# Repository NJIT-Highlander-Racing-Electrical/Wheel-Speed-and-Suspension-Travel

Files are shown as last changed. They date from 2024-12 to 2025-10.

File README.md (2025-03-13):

# Wheel Speed Sensors

The 2024-2025 vehicle will be integrating sprag clutches into each of the four wheels. This allows for all four wheels to be fully locked together when power is applied, but all four wheels to be fully unlocked while coasting. There are numerous benefits to this setup that are not relevant to this project, however they present the need for individual wheel speed sensors.

These sensors provide data to the suspension subteam about how each wheel is rotating as we move through corners. Along with other vehicle data such as yaw rate, GPS position, vehicle velocity, and steering angle, suspension can get a better picture of how these sprag clutches affect vehicle performance. 

## Potential Designs

With the sprag clutches, the wheels, wheel hubs, and brake rotor all spin together. However, this rotational speed can differ from that of the axles when the clutches are in use. Thus, the sensor must detect either wheel, wheel hub, or rotor rotation.

### Gear Tooth/Ferrous Metal Target Sensor (chosen design)

These type of sensors (like the gear tooth speed sensors we have in stock -- [datasheet here](https://www.jameco.com/Jameco/Products/ProdDS/512401.pdf)) provide a digital output that tracks ferrous metal targets. Their datasheet states that they can be used for detecting holes in rotating discs, such as a brake rotor. Using the brake rotor is ideal for this situation as it does not require adding any additional hardware (such as magnets or a trigger wheel), and it actually reduces the weight of the rotor.

The ones we have in stock are no longer for sale, but [these GS100701](https://www.digikey.com/en/products/detail/zf-electronics/GS100701/280932) could work.

It seems best fit to put four holes in the edge of the rotor that will be detected by this sensor. This sensor can be mounted to a tab/bracket on the caliper, and its distance to the rotor can be adjusted using the sensor's threads/nuts. Because the rotor/caliper distances never change, we can get the sensor close enough to the rotor for accurate readings. 

Adding more than 1 hole in the edge of the rotor allows for more accurate readings. At slower speeds, there will only be a few readings per second which does not paint the most accurate picture of the true wheel speed. More than four holes could be added if the sensor/microcontroller is capable of higher polling rates.

### Permanent magnets and hall effects

If one or more permanent magnets are attached to the wheel, we can use a hall effect to detect when this magnetic field passed by. However, this means we must find a way to securely attach the magnets so that they do not fall off while spinning. Magnets also run the risk of being damaged

### Lasers/Infrared

These could be used to detect when a white stripe passes by the emitter/receiver pair (like the CVT tachometer), but dirt, mud, and other substances can cover the sensors or the sensing target.

# Suspension Travel Sensors

The 2024-2025 vehicle will also be integrating four linear suspension travel sensors. These will give an analog reading which represents the linear position of the shocks. We can then use this data to extrapolate the displacement of the wheels. We are using the LPPS-22-200 sensors from HGSI which have a 200mm stroke. They are essentially just a linear potentiometer, so they can be used with a variety of supply voltages.

## Mapping Suspension Position to Wheel Displacement

Fron two shocks have a motion ratio of 0.75, meaning that a travel 0f 0.75" in the shock would correspond to 1" of wheel displacement

# Electrical Design

These eight sensors (four wheel speed and four suspension travel) can be run to a single microcontroller located inside the vehicle, which can then transmit the data over CAN. Ideally, each wheel speed sensor reading is interrupt-based on the microcontroller so that calculations for RPM can be done as fast as possible. Suspension travel are analog so we will simply poll those for values Each sensor (at the enclosure side) has 3 pin aviation plug connectors. This prevents them from accidentally being connected to the general power/CAN bus while still maintaing our aviation plug standard. At the sensor side, each sensor uses a different, smaller in-line 3 pin connector so that the sensors themselves can be removed and replaced without removing the entire wiring harness.

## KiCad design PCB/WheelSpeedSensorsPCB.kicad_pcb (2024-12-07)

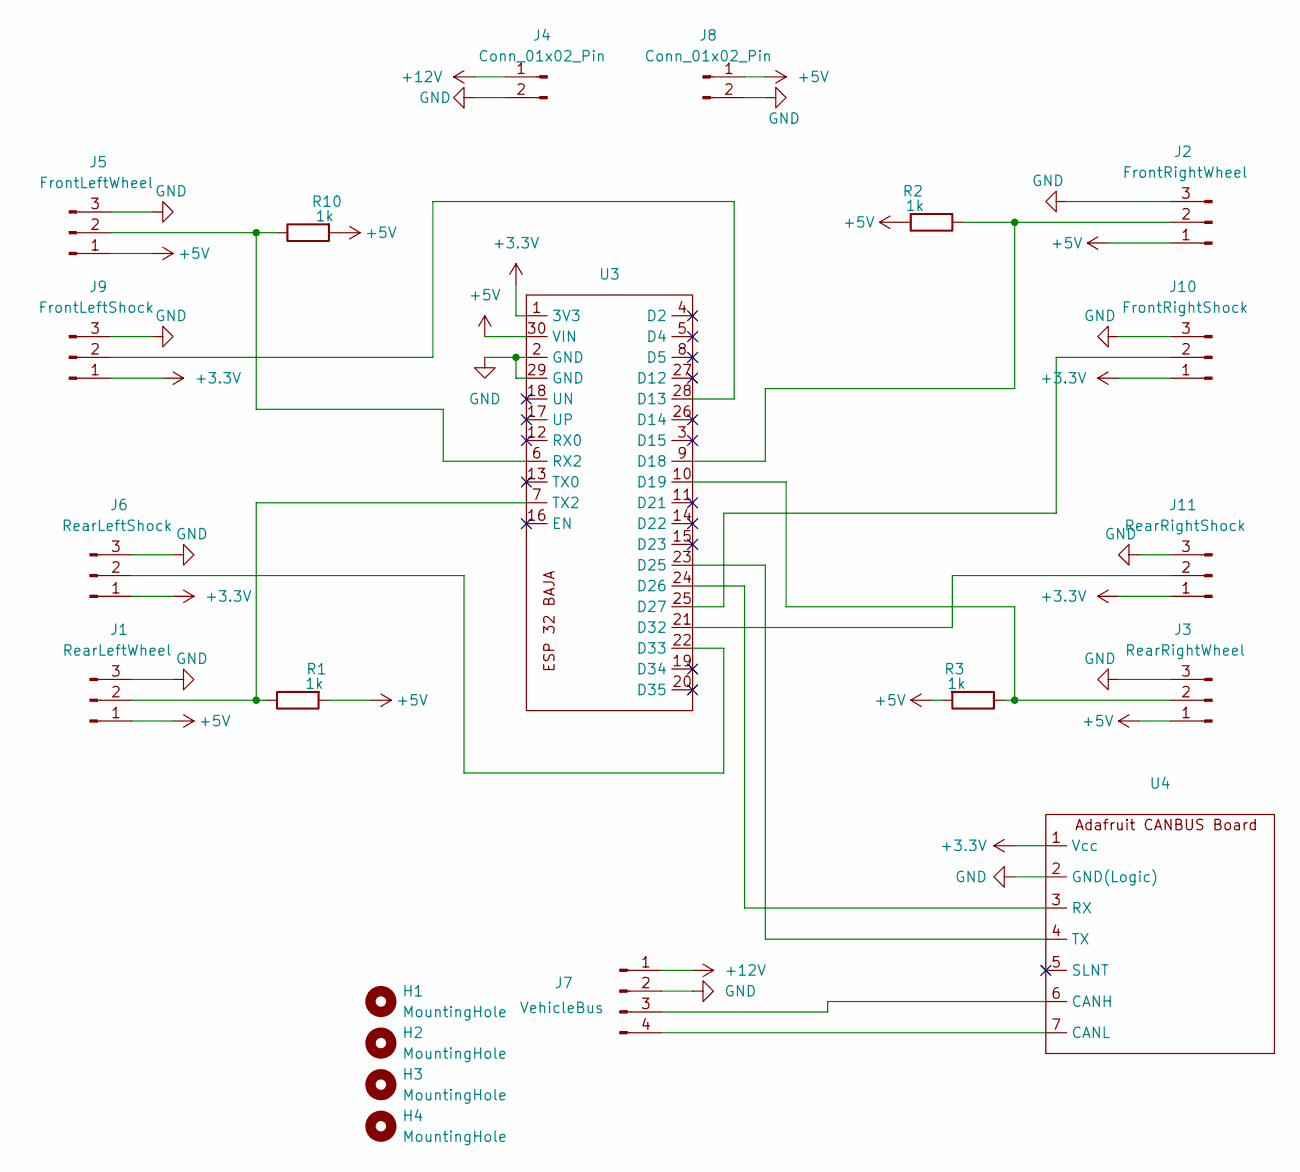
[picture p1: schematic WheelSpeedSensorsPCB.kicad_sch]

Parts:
H1, H2, H3, H4: MountingHole; MountingHole_4.3mm_M4
J1: RearLeftWheel; 3pin
J2: FrontRightWheel; 3pin
J3: RearRightWheel; 3pin
J4, J8: Conn_01x02_Pin; PinHeader_1x02_P2.54mm_Vertical
J5: FrontLeftWheel; 3pin
J6: RearLeftShock; 3pin
J7: VehicleBus; 4pin
J9: FrontLeftShock; 3pin
J10: FrontRightShock; 3pin
J11: RearRightShock; 3pin
R1, R2, R3, R10: 1k; R_Axial_DIN0204_L3.6mm_D1.6mm_P5.08mm_Horizontal
U3: ESP32
U4: 1x7 Connectors

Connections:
+3.3V: J6.1, J9.1, J10.1, J11.1, U3.1 (3V3), U4.1 (Vcc)
+5V: J1.1, J2.1, J3.1, J5.1, J8.1, R1.2, R2.2, R3.2, R10.2, U3.30 (VIN)
+12V: J4.1, J7.1
GND: J1.3, J2.3, J3.3, J4.2, J5.3, J6.3, J7.2, J8.2, J9.3, J10.3, J11.3, U3.2 (GND), U3.29 (GND), U4.2 (GND(Logic))
unnamed: J1.2, R1.1, U3.7 (TX2)
unnamed: J2.2, R2.1, U3.9 (D18)
unnamed: J3.2, R3.1, U3.10 (D19)
unnamed: J5.2, R10.1, U3.6 (RX2)
unnamed: J6.2, U3.22 (D33)
unnamed: J7.3, U4.6 (CANH)
unnamed: J7.4, U4.7 (CANL)
unnamed: J9.2, U3.28 (D13)
unnamed: J10.2, U3.25 (D27)
unnamed: J11.2, U3.21 (D32)
unnamed: U3.23 (D25), U4.4 (TX)
unnamed: U3.24 (D26), U4.3 (RX)

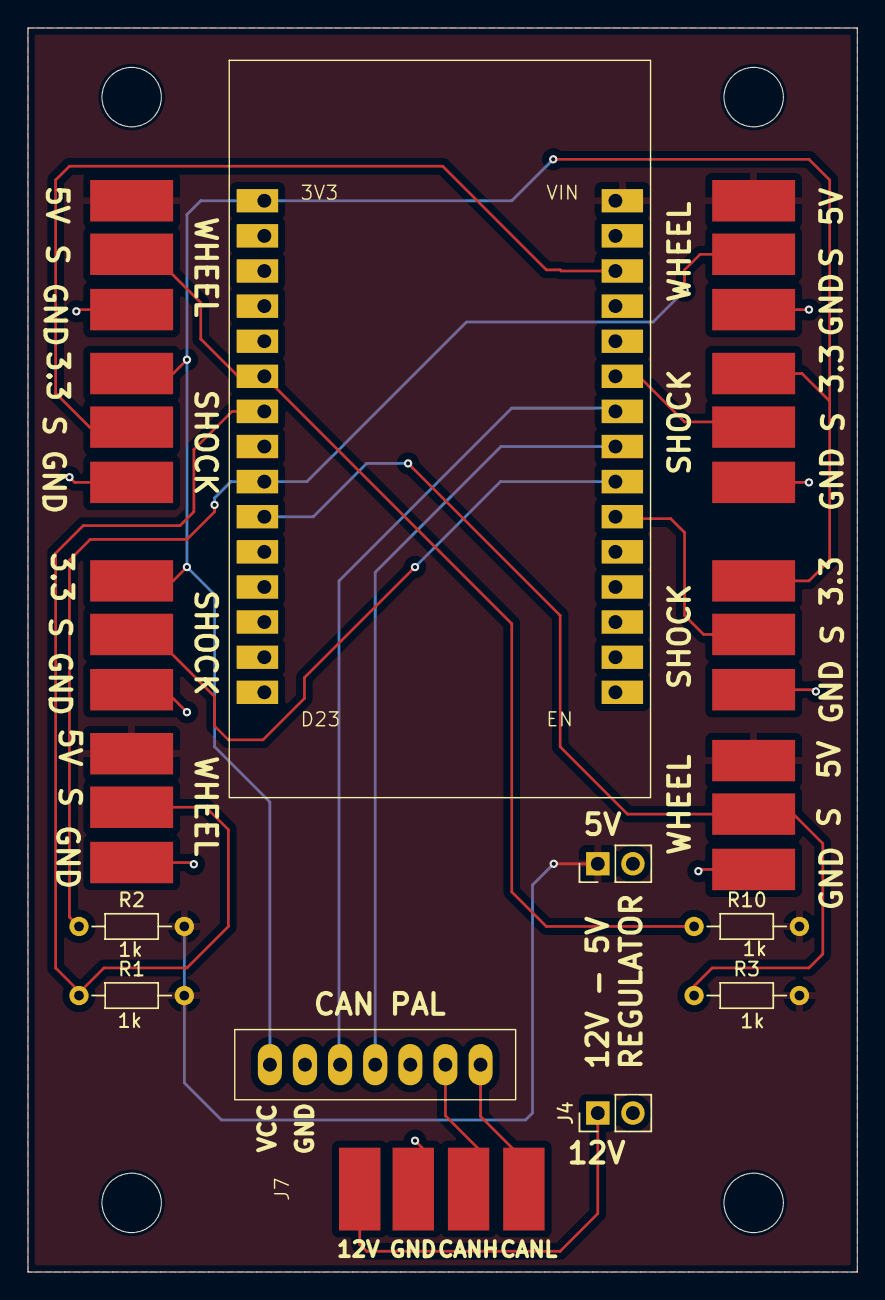
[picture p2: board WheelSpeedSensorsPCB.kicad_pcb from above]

Board: 2 copper layers, 60.0 x 90.0 mm, 21 parts (0 on the bottom side), 16 nets.

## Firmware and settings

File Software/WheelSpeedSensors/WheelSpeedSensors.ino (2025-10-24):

#include "Wheel.h"
#include "Shock.h"
#include "BajaCAN.h"

#define DEBUG_WHEEL false
#define DebugWheelSerial \
  if (DEBUG_WHEEL) Serial

#define DEBUG_SHOCK true
#define DebugShockSerial \
  if (DEBUG_SHOCK) Serial

// Pin definitions for Wheels
const int frontLeftWheelPin = 19;
const int rearLeftWheelPin = 18;
const int frontRightWheelPin = 17;
const int rearRightWheelPin = 16;

// Pin definitions for Shocks
const int frontLeftShockPin = 32;
const int rearLeftShockPin = 27;
const int frontRightShockPin = 33;
const int rearRightShockPin = 13;

// Wheel objects from Wheel.h definition
Wheel frontLeftWheel(frontLeftWheelPin);
Wheel frontRightWheel(frontRightWheelPin);
Wheel rearLeftWheel(rearLeftWheelPin);
Wheel rearRightWheel(rearRightWheelPin);

// Shock objects from Shock.h definition
Shock frontLeftShock(frontLeftShockPin, true, frontLeftShock_restReading);
Shock frontRightShock(frontRightShockPin, true, frontRightShock_restReading);
Shock rearLeftShock(rearLeftShockPin, false, rearLeftShock_restReading);
Shock rearRightShock(rearRightShockPin, false, rearRightShock_restReading);

void setup() {
  Serial.begin(460800);

  delay(100);  // Brief delay for serial to stabilize

  // If the speed sensor detects a metal, it outputs a HIGH. Otherwise, LOW
  // Thus, we want to trigger interrupt on LOW to HIGH transition
  attachInterrupt(digitalPinToInterrupt(frontLeftWheel.sensorPin), frontLeftISR, RISING);
  attachInterrupt(digitalPinToInterrupt(frontRightWheel.sensorPin), frontRightISR, RISING);
  attachInterrupt(digitalPinToInterrupt(rearLeftWheel.sensorPin), rearLeftISR, RISING);
  attachInterrupt(digitalPinToInterrupt(rearRightWheel.sensorPin), rearRightISR, RISING);

  setupCAN(WHEEL_SPEED, 10);  // sendInterval = 10 means that we will be sending 100 times per second

  Serial.println("Wheel Speed System Initialized");
}

void loop() {
  // updateWheelStatus calculates RPM if applicable, checks zero RPM status, and checks for wheelspin/wheel skid
  frontLeftWheel.updateWheelStatus();
  frontRightWheel.updateWheelStatus();
  rearLeftWheel.updateWheelStatus();
  rearRightWheel.updateWheelStatus();

  // Update CAN-Bus variables
  frontLeftWheelSpeed = frontLeftWheel.wheelSpeedMPH;
  frontRightWheelSpeed = frontRightWheel.wheelSpeedMPH;
  rearLeftWheelSpeed = rearLeftWheel.wheelSpeedMPH;
  rearRightWheelSpeed = rearRightWheel.wheelSpeedMPH;

  frontLeftWheelState = frontLeftWheel.wheelState;
  frontRightWheelState = frontRightWheel.wheelState;
  rearLeftWheelState = rearLeftWheel.wheelState;
  rearRightWheelState = rearRightWheel.wheelState;

  // Read shock positions
  frontLeftShock.getPosition();
  frontRightShock.getPosition();
  rearLeftShock.getPosition();
  rearRightShock.getPosition();

  frontLeftDisplacement = frontLeftShock.wheelPos;
  frontRightDisplacement = frontRightShock.wheelPos;
  rearLeftDisplacement = rearLeftShock.wheelPos;
  rearRightDisplacement = rearRightShock.wheelPos;

  // Print data to serial monitor
  DebugWheelSerial.print("frontLeftWheel_Speed:");
  DebugWheelSerial.print(frontLeftWheel.wheelSpeedMPH, 2);
  DebugWheelSerial.print(",");
  DebugWheelSerial.print("frontRightWheel_Speed:");
  DebugWheelSerial.print(frontRightWheel.wheelSpeedMPH, 2);
  DebugWheelSerial.print(",");
  DebugWheelSerial.print("rearLeftWheel_Speed:");
  DebugWheelSerial.print(rearLeftWheel.wheelSpeedMPH, 2);
  DebugWheelSerial.print(",");
  DebugWheelSerial.print("rearRightWheel_Speed:");
  DebugWheelSerial.print(rearRightWheel.wheelSpeedMPH, 2);
  DebugWheelSerial.println();

  DebugShockSerial.print("fl_pos:");
  DebugShockSerial.print(frontLeftShock.wheelPos);
  DebugShockSerial.print(",");
  DebugShockSerial.print("fr_pos:");
  DebugShockSerial.print(frontRightShock.wheelPos);
  DebugShockSerial.print(",");
  DebugShockSerial.print("rl_pos:");
  DebugShockSerial.print(rearLeftShock.wheelPos);
  DebugShockSerial.print(",");
  DebugShockSerial.print("rr_pos:");
  DebugShockSerial.print(rearRightShock.wheelPos);
  DebugShockSerial.println();
}

// ISR implementations - now use the debounced handleInterrupt() method
void frontLeftISR() {
  frontLeftWheel.handleInterrupt();
}

void frontRightISR() {
  frontRightWheel.handleInterrupt();
}

void rearLeftISR() {
  rearLeftWheel.handleInterrupt();
}

void rearRightISR() {
  rearRightWheel.handleInterrupt();
}

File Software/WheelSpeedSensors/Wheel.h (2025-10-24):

const float wheelDiameter = 23;      // Diameter of our wheels in inches
const int targetsPerRevolution = 4;  // number of sensing points per revolution on the wheel
const float wheelSpinThreshold = 5;  // Speed difference (mph) above GPS vehicle velocity where we will declare wheelspin
const float wheelSkidThreshold = 5;  // Speed difference (mph) below GPS vehicle velocity where we will declare skidding

const float rpmToMphFactor = wheelDiameter / 63360.0 * 3.1415 * 60.0;  // When wheel RPM is multiplied by this, it results in that wheel's linear speed in MPH

float vehicleSpeedMPH = 0;  // Since GPS velocity is given in m/s, this converts and stores to MPH

// Minimum time between valid readings (microseconds) - prevents noise/bouncing
// 5000us = 5ms = maximum 720 RPM (well above expected max)
const unsigned long MIN_PULSE_INTERVAL = 5000;

// Maximum time to wait before declaring zero RPM
// At 1 MPH with 4 targets, we get a pulse every ~1.03 seconds
// Allow 2 seconds (2,000,000 microseconds) before declaring zero
const unsigned long ZERO_TIMEOUT_MICROS = 2000000;

enum WheelState {
  GOOD,
  SPIN,
  SKID
};

// Class that defines shared variables and functions between the four wheels
class Wheel {

public:

  int sensorPin;  // GPIO that sensor is hooked up to

  volatile unsigned long lastReadingMicros;
  volatile unsigned long currentReadingMicros;
  volatile bool updateFlag;

  unsigned long nextExpectedMicros;
  
  float rpm;  // variable to store calculated RPM value
  float wheelSpeedMPH;  // calculated wheel velocity for comparison with GPS vehicle velocity

  bool ignoreNextReading;
  bool isFirstReading;

  WheelState wheelState;

  // Moving average for stability
  static const int AVG_SAMPLES = 3;
  float rpmHistory[AVG_SAMPLES];
  int rpmHistoryIndex;
  int rpmHistoryCount;  // Track how many samples we have

  Wheel(int pinNumber) {
    sensorPin = pinNumber;
    unsigned long currentTime = micros();
    lastReadingMicros = currentTime;
    currentReadingMicros = currentTime;
    nextExpectedMicros = currentTime + ZERO_TIMEOUT_MICROS;
    rpm = 0;
    wheelSpeedMPH = 0;
    updateFlag = false;
    ignoreNextReading = false;
    isFirstReading = true;
    wheelState = GOOD;
    rpmHistoryIndex = 0;
    rpmHistoryCount = 0;

    // Initialize RPM history to zero
    for(int i = 0; i < AVG_SAMPLES; i++) {
      rpmHistory[i] = 0;
    }

    pinMode(sensorPin, INPUT);
  }

  // Calculates RPM based on elapsed time between last reading and current time
  // Only runs after respective ISR is triggered
  void calculateRPM() {
    if (!updateFlag) return;

    // Capture timing variables atomically to avoid race conditions
    noInterrupts();
    unsigned long capturedCurrent = currentReadingMicros;
    unsigned long capturedLast = lastReadingMicros;
    updateFlag = false;
    interrupts();

    // Skip first reading - need two points to calculate speed
    if (isFirstReading) {
      noInterrupts();
      lastReadingMicros = capturedCurrent;
      interrupts();
      isFirstReading = false;
      nextExpectedMicros = capturedCurrent + ZERO_TIMEOUT_MICROS;
      return;
    }

    // If we just recovered from zero, ignore this reading (re-establish baseline)
    if (ignoreNextReading) {
      noInterrupts();
      lastReadingMicros = capturedCurrent;
      interrupts();
      ignoreNextReading = false;
      nextExpectedMicros = capturedCurrent + ZERO_TIMEOUT_MICROS;
      return;
    }

    // Calculate time difference (handles overflow correctly since both are unsigned long)
    unsigned long timeDifference = capturedCurrent - capturedLast;
    
    // Sanity check: reject readings that are too fast (noise/bounce filter)
    if (timeDifference < MIN_PULSE_INTERVAL) {
      return;
    }
    
    // Sanity check: reject readings that are impossibly slow (missed timeout somehow)
    if (timeDifference > ZERO_TIMEOUT_MICROS) {
      noInterrupts();
      lastReadingMicros = capturedCurrent;
      interrupts();
      ignoreNextReading = true;
      return;
    }
    
    // Calculate RPM from time difference
    float instantRPM = (1.00 / (float(timeDifference) / 1000000.0)) * 60.0 / targetsPerRevolution;
    
    // Sanity check: 650 RPM = ~45 MPH, reasonable maximum
    if (instantRPM > 650) {
      Serial.print("RPM over 650 rejected: ");
      Serial.print(instantRPM);
      Serial.print(" on pin ");
      Serial.println(sensorPin);
      return;
    }
    
    // Add to moving average buffer
    rpmHistory[rpmHistoryIndex] = instantRPM;
    rpmHistoryIndex = (rpmHistoryIndex + 1) % AVG_SAMPLES;
    if (rpmHistoryCount < AVG_SAMPLES) {
      rpmHistoryCount++;
    }
    
    // Calculate average RPM
    float sum = 0;
    for(int i = 0; i < rpmHistoryCount; i++) {
      sum += rpmHistory[i];
    }
    rpm = sum / rpmHistoryCount;
    
    // Convert to MPH
    wheelSpeedMPH = rpm * rpmToMphFactor;
    
    // Update timing for next expected reading (with 2x buffer for timeout detection)
    nextExpectedMicros = capturedCurrent + (timeDifference * 2);
    
    // Update last reading time atomically
    noInterrupts();
    lastReadingMicros = capturedCurrent;
    interrupts();
  }

  // Checks to see if a certain period of time has passed since last reading
  // If we surpass that threshold, set the RPM to zero
  void checkZeroRPM() {
    // Don't check if we haven't established baseline yet
    if (isFirstReading || ignoreNextReading) return;
    
    unsigned long currentTime = micros();
    
    // Check if we've exceeded the expected next reading time
    // This handles overflow correctly: if currentTime wraps around,
    // the subtraction still works due to unsigned arithmetic properties
    unsigned long timeSinceLastReading = currentTime - lastReadingMicros;
    
    if (timeSinceLastReading > ZERO_TIMEOUT_MICROS) {
      // No readings in too long - wheel has stopped
      
      // Reset all state atomically
      noInterrupts();
      lastReadingMicros = currentTime;
      interrupts();
      
      ignoreNextReading = true;  // Next reading will be used to re-establish baseline
      rpm = 0;
      wheelSpeedMPH = 0;
      nextExpectedMicros = currentTime + ZERO_TIMEOUT_MICROS;
      
      // Clear RPM history
      for(int i = 0; i < AVG_SAMPLES; i++) {
        rpmHistory[i] = 0;
      }
      rpmHistoryIndex = 0;
      rpmHistoryCount = 0;
    }
  }

  // Compares wheel speed to GPS vehicle speed to see if we have wheelspin or skidding
  void checkWheelState() {
    // Only check wheel state if we have valid GPS data
    if (vehicleSpeedMPH < 0.1) {
      wheelState = GOOD;  // Don't declare spin/skid at very low speeds
      return;
    }
    
    float speedDifference = wheelSpeedMPH - vehicleSpeedMPH;
    
    if (speedDifference > wheelSpinThreshold) {
      wheelState = SPIN;
    } else if (speedDifference < -wheelSkidThreshold) {
      wheelState = SKID;
    } else {
      wheelState = GOOD;
    }
  }
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

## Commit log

2024-09-15 add link to new speed hall sensors
2024-09-16 move arduino test file inside of a proper folder
2024-10-24 Set targetsPerRevolution to 8 for front rotor
2024-11-15 Add first iteration enclosure files
2024-11-17 Update Enclosure
2024-11-18 Add first version of PCB
    [WheelSpeedSensorsPCB.kicad_pcb, WheelSpeedSensorsPCB.kicad_sch]
2024-11-20 Fix schematic/PCB to use proper CAN TX and RX pins
    [WheelSpeedSensorsPCB.kicad_pcb, WheelSpeedSensorsPCB.kicad_sch]
2024-11-20 Fix minor issue with trace to GPIO 26
    [WheelSpeedSensorsPCB.kicad_pcb]
2024-11-20 Add gerber and drill files for PCBWay
2024-11-21 Update PCB and GBRs to have Silkscreen
    [WheelSpeedSensorsPCB.kicad_pcb]
2024-11-21 Fix silkscreen mistake on vehicle bus connection
    [WheelSpeedSensorsPCB.kicad_pcb]
2024-11-21 Delete PCB/GRB_Files_v1_11_20_2024.zip
    Old files
2024-11-30 Major updates to structure and logic
    Add class for all four wheels
    Add spin/skid code
    Improve ISR execution
2024-12-05 Minor fixes to wheel revolution calculations
    [WheelSpeedSensors.ino]
2024-12-05 IMPORTANT: Fix reversed 5V/GND silkscreen
    On the right side of the PCB, the 5V and GND silkscreens were reversed for the wheel speed sensors. This does not interfere with the usage of the board, but it is important to note when wiring
    [WheelSpeedSensorsPCB.kicad_pcb]
2024-12-05 Update footprints to better fit standard resistors
    [WheelSpeedSensorsPCB.kicad_pcb]
2024-12-06 Add framework for wheel displacement lookup table
2024-12-07 Fix silkscreen errors on left side shocks
    [WheelSpeedSensorsPCB.kicad_pcb]
2024-12-24 Update debug print statements
2025-01-06 Update Subsystem to use latest CAN driver
2025-01-06 Update program to use latest CAN driver
2025-01-07 Update to latest CAN driver
2025-01-07 Update BajaCAN.h for RTRs
    This update adds the necessary code to the BajaCAN.h file for all subsystems to receive and process any RTRs sent to them. It also adds some test code to the Wheel Speed section that will eventually 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
2025-02-12 Fix bug where rearLeftShock position was not being updated
    [WheelSpeedSensors.ino]
2025-02-26 Add first version of 3D model
    This model includes a plastic part version that uses threaded inserts and a metal 3d printed version that has undersized holes for tapping threads
    [Suspension Travel Sensor Mount v3.f3z]
2025-02-28 Update Model Names and Update to latest design
    [Suspension Travel Sensor Metal 3D Printed Mount_.step, Suspension Travel Sensor Mount v3.f3z]
2025-03-01 Make height shorter for Metal 3D Printing
    [Suspension Travel Sensor Metal 3D Printed Mount.step, Suspension Travel Sensor Metal 3D Printed Mount_.step]
2025-03-14 Updates
    Add new code for motion ratio, fix some convention issues
    [Shock.h, WheelSpeedSensors.ino]
2025-03-29 Module now prints inches to CAN bus instead of analog val
2025-04-19 Update 3D models
    [Suspension Travel Sensor Metal 3D Printed Mount.step]
2025-04-24 Update variables to match new mounting orientation on vehicle
2025-05-02 Several updates, see desc
    Update all Wheel RPM variables to wheel Speed MPH
    Update to latest CAN driver (also related to this RPM->MPH change)
    This driver changes what data the wheel speed sensors send
    Update rpmToMphFactor to prevent possible float rounding
    [Wheel.h, WheelSpeedSensors.ino]
2025-05-10 change debug print from shock pos to wheel pos
2025-05-10 Fix bug where wheel speed was not resetting after last reading
    [Wheel.h]
2025-05-10 Fix bug where readings would jump to 93MPH in certain occasions
    [Wheel.h]
2025-05-10 Actually fix the bug
    [Wheel.h]
2025-05-11 Wheel Speed seems to be packet offender
    Trying to move setup CAN to see if that helps
2025-06-08 Fix bug where motion ratio was reversed
    I was multiplying the shock position by the motion ratio to get wheel position, when in reality I should have been dividing. A motion ratio of 0.75 means that the shock will only move 0.75" for every 1" that the wheel travels, not vice versa
    [Shock.h]
2025-06-13 update rest readings for new springs
2025-06-13 Fix direction of wheel position data
    [Shock.h, WheelSpeedSensors.ino]
2025-06-14 Fix wheel speed zeroing method
    This code updates the zeroing based on the last reading and the next expected reading time, plus a small buffer to account for a slowing down vehicle. The previous version worked based solely off a static 1 second elapsed time
    [Wheel.h]
2025-06-14 Comment out testing Serial prints
2025-08-02 Fixed suspenion displacement data not sending
    The parse float function reads data until a delimiter, but CAN.print does not always send a delimiter. I don't know what CAN.endpacket does. Updated to CAN.println to make it work.
    Note that the only other stuff using CAN.parseFloat is the floats from the DAS. Everything else is INTs. Nothing actually reads DAS data like acceleration or GPS, which is why we haven't seen this issue elsewhere
    [Wheel.h, WheelSpeedSensors.ino]
2025-08-02 Fix serial prints taht should have been debug prints
    [Wheel.h]
2025-08-02 Nevermind, cant use DEBUG WHEEL Macros in .h file, just commenting them out
2025-08-02 attempt to go from println to print and print('\n'). also add short delays between messages. maybe parsefloat() is slow idk
2025-08-02 Fixed the code. Thanks Claude
    [Wheel.h, WheelSpeedSensors.ino]
2025-09-07 Fix timeout bug while sending float in BajaCAN.h
    [BajaCAN.h]
